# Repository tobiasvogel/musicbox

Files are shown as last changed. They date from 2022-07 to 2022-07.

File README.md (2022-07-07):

# MIDI Music Box

This is an improved version of the original musicbox project by [mitxela](https://github.com/mitxela/musicbox).

There are two major enhancements over the original version:
 - PCBs (Gerber and EAGLE) for the circuits as well as most of the mechanical parts
 - A (optional) addon-board featuring a Arduino MKR WiFi 1010 providing MIDI-file support from both microSD-cards and via WiFi (Webbrowser)

In the future I will furthermore add:
 * *BOM for all PCBs* (work-in-progress)
 * Renderings for visualization
 * Detailed assembly instructions

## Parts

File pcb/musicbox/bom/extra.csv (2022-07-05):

Part | Value | Package | Description | DIGIKEY_PART_NUMBER | FARNELL_PART_NUMBER | MANUFACTURER_NAME | MOUSER_PART_NUMBER
*J2 |  |  | Wire Housings HSG 3P WITH LKG RAMP | WM2012-ND | 1462834 | Molex | 538-22-01-2037
*J3 |  |  | Wire Housings HSG 2P WITH LKG RAMP | WM2011-ND | 1654528 | Molex | 538-22-01-2027
*J4 |  |  | Wire Housings HSG 2P WITH LKG RAMP | WM2011-ND | 1654528 | Molex | 538-22-01-2027
*J5 |  |  | Wire Housings HSG 5P WITH LKG RAMP | WM2014-ND | 1756788 | Molex | 538-22-01-2057
*OK1 |  | DIP08 | 8P IC SOCKET | 609-4717-ND | 2668407 | Amphenol FCI | 649-DILB8P223TLF
*SV1 | Servos 01-15 | Female IDC Socket | HARTING | 0918516681358U-ND | 1106729 | Harting | 617-09-18-516-6813
*SV2 | Servos 16-30 | Female IDC Socket | HARTING | 0918516681358U-ND | 1106729 | Harting | 617-09-18-516-6813
*SV1 | Servos 01-15 | 16P | 3M IDC Flat Cable | 3M157816-1-ND |  | 3M | 3365/16-CUT-LENGTH
*SV2 | Servos 16-30 | 16P | 3M IDC Flat Cable | 3M157816-1-ND |  | 3M | 3365/16-CUT-LENGTH
*U$1 |  | SIP20 | 20P SIP SOCKET | 952-1905-ND | 7991967 | Harwin | 855-M20-7822046
*U$1 |  | SIP20 | 20P SIP SOCKET | 952-1905-ND | 7991967 | Harwin | 855-M20-7822046
*U$1 |  | SIP4 | 4P SIP SOCKET | 952-1792-ND | 7991932 | Harwin | 855-M20-7820446
*ST-LINK |  |  |  | 952-2276-ND | 3395117 | Harwin | 855-M22-2010505

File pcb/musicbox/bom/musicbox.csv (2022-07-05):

Part | Value | Package | Description | DIGIKEY_PART_NUMBER | FARNELL_PART_NUMBER | MANUFACTURER_NAME | MOUSER_PART_NUMBER
C1 | 100nF | C025-025X050 | CAPACITOR, European symbol | BC5142-ND | 2112909 | Vishay / BC Components | 594-K104M15X7RF53L2
D1 | 1N4148 | DO35-7 | DIODE | 1N4148FS-ND | 2322485 | Onsemi / Fairchild | 512-1N4148
D2 | 1N4004 | DO41-10 | DIODE | 1N4004MSCT-ND | 1843708 | Rectron | 583-1N4004-T
J1 | 1727010 | 1727010 | Conn PC Terminal Block 2 POS 3.81mm Solder ST Thru-Hole 13.5A | 277-1947-ND | 3704579 | Phoenix Contact | 651-1727010
J2 | 22-27-2031-03 | 6410-03 | CONNECTOR | WM4112-ND | 9731156 | Molex | 538-22-27-2031
J3 | 22-27-2021-02 | 6410-02 | CONNECTOR | WM4111-ND | 9731148 | Molex | 538-22-27-2021
J4 | 22-27-2021-02 | 6410-02 | CONNECTOR | WM4111-ND | 9731148 | Molex | 538-22-27-2021
J5 | 22-27-2051-05 | 6410-05 | CONNECTOR | WM4114-ND | 9731679 | Molex | 538-22-27-2051
JP1 | HANDLE-MOTOR | 1X03 | PIN HEADER | 68004-403-ND | 3881564 | Amphenol FCI | 651-1012937890301BLF
OK1 | 6N137 | DIL08 | MOTOROLA OPTO COUPLER | 160-1791-ND | 1328376 | Lite-On | 859-6N137
R1 | 220? | 0207/7 | RESISTOR, European symbol | BC3666CT-ND | 3546954 | Vishay / Beyschlag | 594-MBB02070C2200FCT
R2 | 470? | 0207/7 | RESISTOR, European symbol | BC3790CT-ND | 3547014 | Vishay / Beyschlag | 594-MBB02070C4700FCT
ST-LINK | M22-7130542 | RHDR5W50P0X200_1X5_1050X240X44 | 2mm pitch, SIL vertical socket assembly, 5 position | 952-1352-5-ND | 1109729 | Harwin | 855-M22-7130542
SV1 | Servos 01-15 | ML16 | HARTING | 1195-1694-ND | 1106834 | Harting | 617-09185166324
SV2 | Servos 16-30 | ML16 | HARTING | 1195-1694-ND | 1106834 | Harting | 617-09185166324
T1 | 2N2222 | TO92 | NPN TRANSISTOR | KSP2222ABUFS-ND | 1700711 | Diotec Semiconductors | 637-2N2222A
U$1 | STM32F103C8T6 | STM32F103C8T6 | Blue Pill Development Board

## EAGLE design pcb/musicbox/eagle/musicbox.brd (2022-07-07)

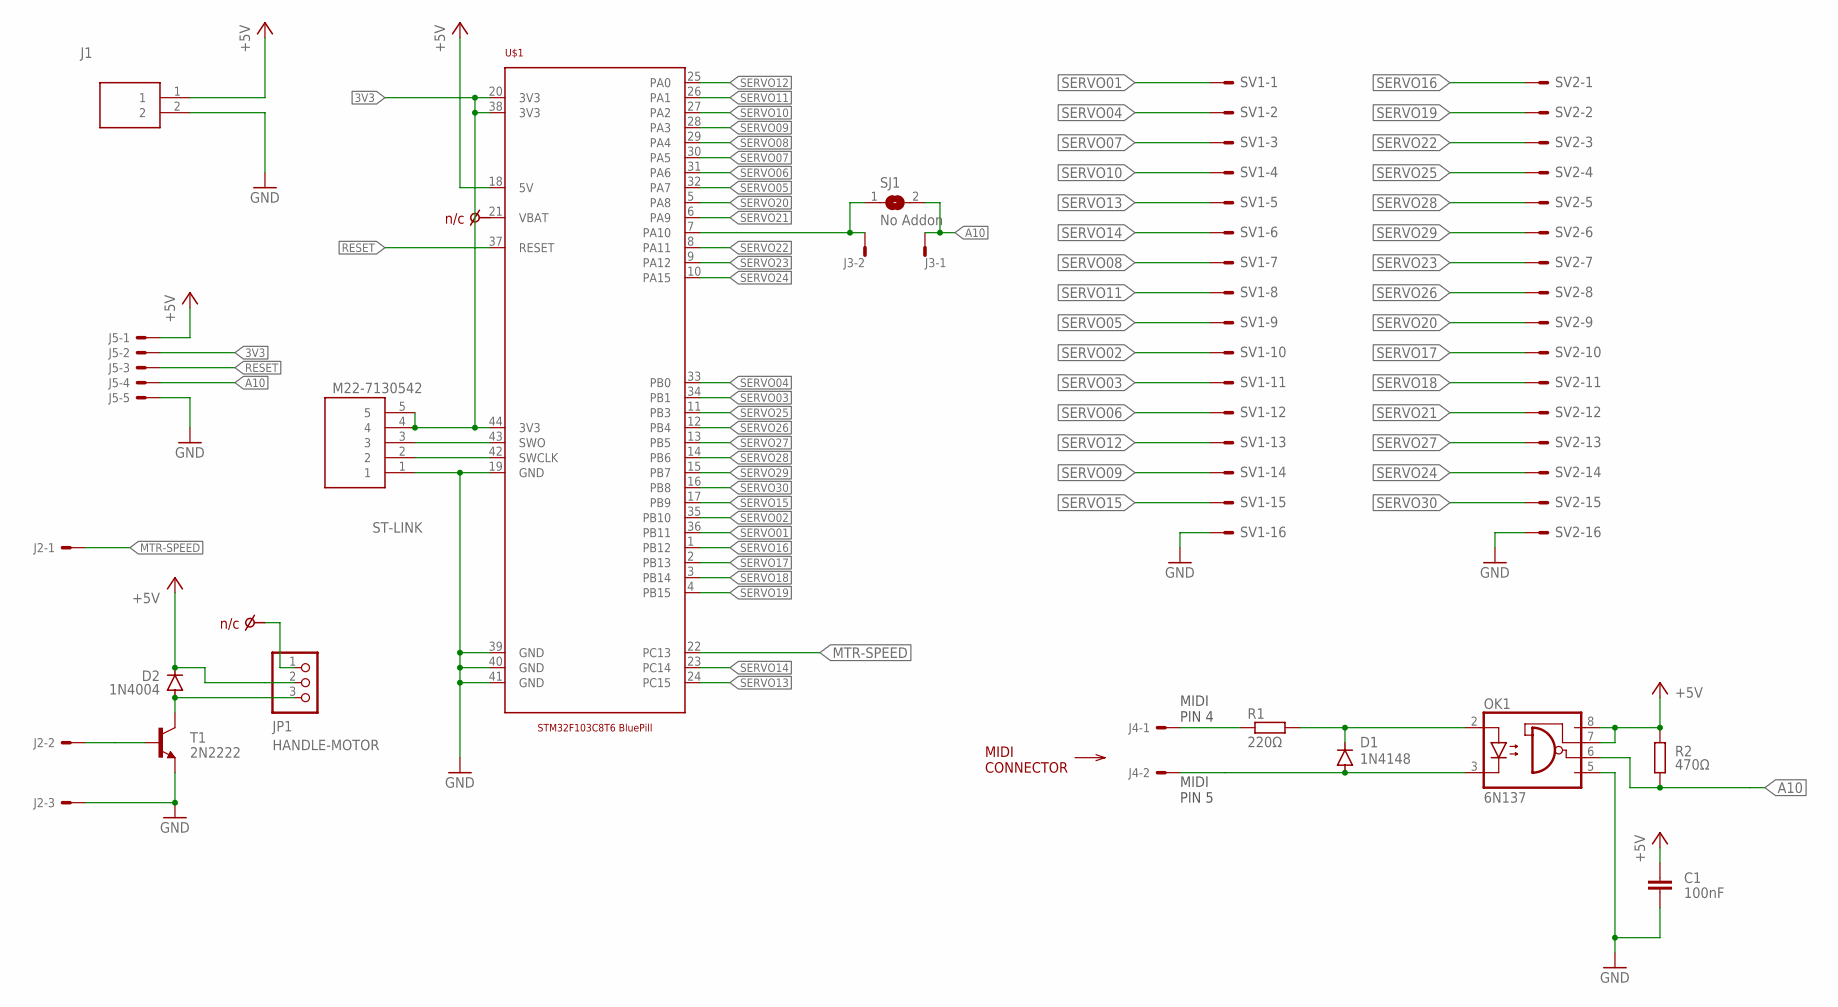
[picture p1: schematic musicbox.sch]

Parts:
C1: 100nF; C025-025X050; MOUSER_PART_NUMBER 594-K104M15X7RF53L2; DIGIKEY_PART_NUMBER BC5142-ND
D1: 1N4148; DO35-7; MOUSER_PART_NUMBER 512-1N4148; DIGIKEY_PART_NUMBER 1N4148FS-ND
D2: 1N4004; DO41-10; MOUSER_PART_NUMBER 583-1N4004-T; DIGIKEY_PART_NUMBER 1N4004MSCT-ND
J1: 1727010; DIGIKEY_PART_NUMBER 277-1947-ND
J2: 22-27-2031-03; 6410-03; MOUSER_PART_NUMBER 538-22-27-2031; DIGIKEY_PART_NUMBER WM4112-ND
J3, J4: 22-27-2021-02; 6410-02; MOUSER_PART_NUMBER 538-22-27-2021; DIGIKEY_PART_NUMBER WM4111-ND
J5: 22-27-2051-05; 6410-05; MOUSER_PART_NUMBER 538-22-27-2051; DIGIKEY_PART_NUMBER WM4114-ND
JP1: HANDLE-MOTOR; 1X03; MOUSER_PART_NUMBER 651-1012937890301BLF; DIGIKEY_PART_NUMBER 68004-403-ND
OK1: 6N137; DIL08; MOUSER_PART_NUMBER 859-6N137; DIGIKEY_PART_NUMBER 160-1791-ND
R1: 220Ω; 0207/7; MOUSER_PART_NUMBER 594-MBB02070C2200FCT; DIGIKEY_PART_NUMBER BC3666CT-ND
R2: 470Ω; 0207/7; MOUSER_PART_NUMBER 594-MBB02070C4700FCT; DIGIKEY_PART_NUMBER BC3790CT-ND
SJ1: No Addon; SJW
ST-LINK: M22-7130542; RHDR5W50P0X200_1X5_1050X240X44; DIGIKEY_PART_NUMBER 952-1352-5-ND
SV1: Servos 01-15; ML16; MOUSER_PART_NUMBER 617-09185166324; DIGIKEY_PART_NUMBER 1195-1694-ND
SV2: Servos 16-30; ML16; MOUSER_PART_NUMBER 617-09185166324; DIGIKEY_PART_NUMBER 1195-1694-ND
T1: 2N2222; TO92; MOUSER_PART_NUMBER 637-2N2222A; DIGIKEY_PART_NUMBER KSP2222ABUFS-ND
U$1: STM32F103C8T6BLUEPILL; STM32F103C8T6

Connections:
3V3: J5.2, ST-LINK.4, ST-LINK.5, U$1.20 (3V3), U$1.38 (3V3), U$1.44 (3V3)
+5V: C1.1, D2.C, J1.1, J5.1, JP1.2, OK1.7 (VE), OK1.8 (VCC), R2.2, U$1.18 (5V)
A10: J3.1, J5.4, OK1.6 (VO), R2.1, SJ1.2
CLK: ST-LINK.2, U$1.42 (SWCLK)
DIO: ST-LINK.3, U$1.43 (SWO)
GND: C1.2, J1.2, J2.3, J5.5, OK1.5 (GND), ST-LINK.1, SV1.16, SV2.16, T1.3 (E), U$1.19 (GND), U$1.39 (GND), U$1.40 (GND), U$1.41 (GND)
MTR-SPEED: J2.1, U$1.22 (PC13)
unnamed: J2.2, T1.2 (B)
unnamed: J4.1, R1.1
unnamed: D2.A, JP1.3, T1.1 (C)
unnamed: D1.A, J4.2, OK1.3 (C)
unnamed: D1.C, OK1.2 (A), R1.2
unnamed: J3.2, SJ1.1, U$1.7 (PA10)
RESET: J5.3, U$1.37 (RESET)
SERVO01: SV1.1, U$1.36 (PB11)
SERVO02: SV1.10, U$1.35 (PB10)
SERVO03: SV1.11, U$1.34 (PB1)
SERVO04: SV1.2, U$1.33 (PB0)
SERVO05: SV1.9, U$1.32 (PA7)
SERVO06: SV1.12, U$1.31 (PA6)
SERVO07: SV1.3, U$1.30 (PA5)
SERVO08: SV1.7, U$1.29 (PA4)
SERVO09: SV1.14, U$1.28 (PA3)
SERVO10: SV1.4, U$1.27 (PA2)
SERVO11: SV1.8, U$1.26 (PA1)
SERVO12: SV1.13, U$1.25 (PA0)
SERVO13: SV1.5, U$1.24 (PC15)
SERVO14: SV1.6, U$1.23 (PC14)
SERVO15: SV1.15, U$1.17 (PB9)
SERVO16: SV2.1, U$1.1 (PB12)
SERVO17: SV2.10, U$1.2 (PB13)
SERVO18: SV2.11, U$1.3 (PB14)
SERVO19: SV2.2, U$1.4 (PB15)
SERVO20: SV2.9, U$1.5 (PA8)
SERVO21: SV2.12, U$1.6 (PA9)
SERVO22: SV2.3, U$1.8 (PA11)
SERVO23: SV2.7, U$1.9 (PA12)
SERVO24: SV2.14, U$1.10 (PA15)
SERVO25: SV2.4, U$1.11 (PB3)
SERVO26: SV2.8, U$1.12 (PB4)
SERVO27: SV2.13, U$1.13 (PB5)
SERVO28: SV2.5, U$1.14 (PB6)
SERVO29: SV2.6, U$1.15 (PB7)
SERVO30: SV2.15, U$1.16 (PB8)

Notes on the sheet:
MIDI PIN 5
MIDI PIN 4
MIDI CONNECTOR

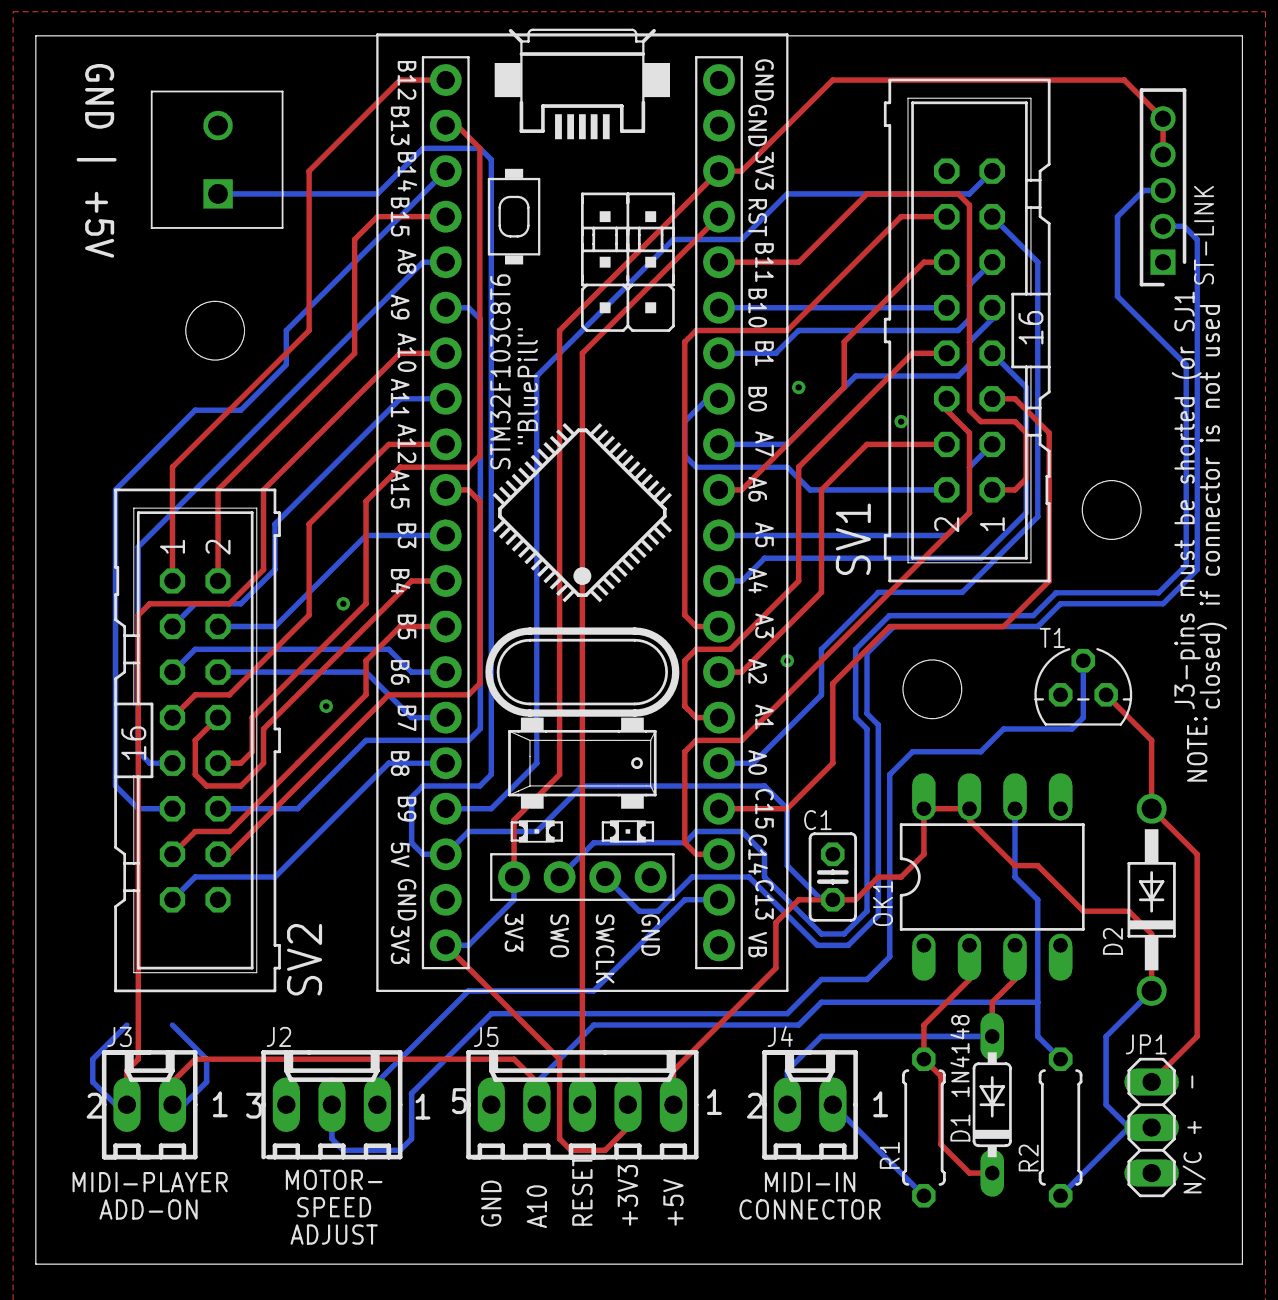
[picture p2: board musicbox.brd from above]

Board: 2 copper layers, 67.3 x 68.5 mm, 18 parts (1 on the bottom side), 44 nets.

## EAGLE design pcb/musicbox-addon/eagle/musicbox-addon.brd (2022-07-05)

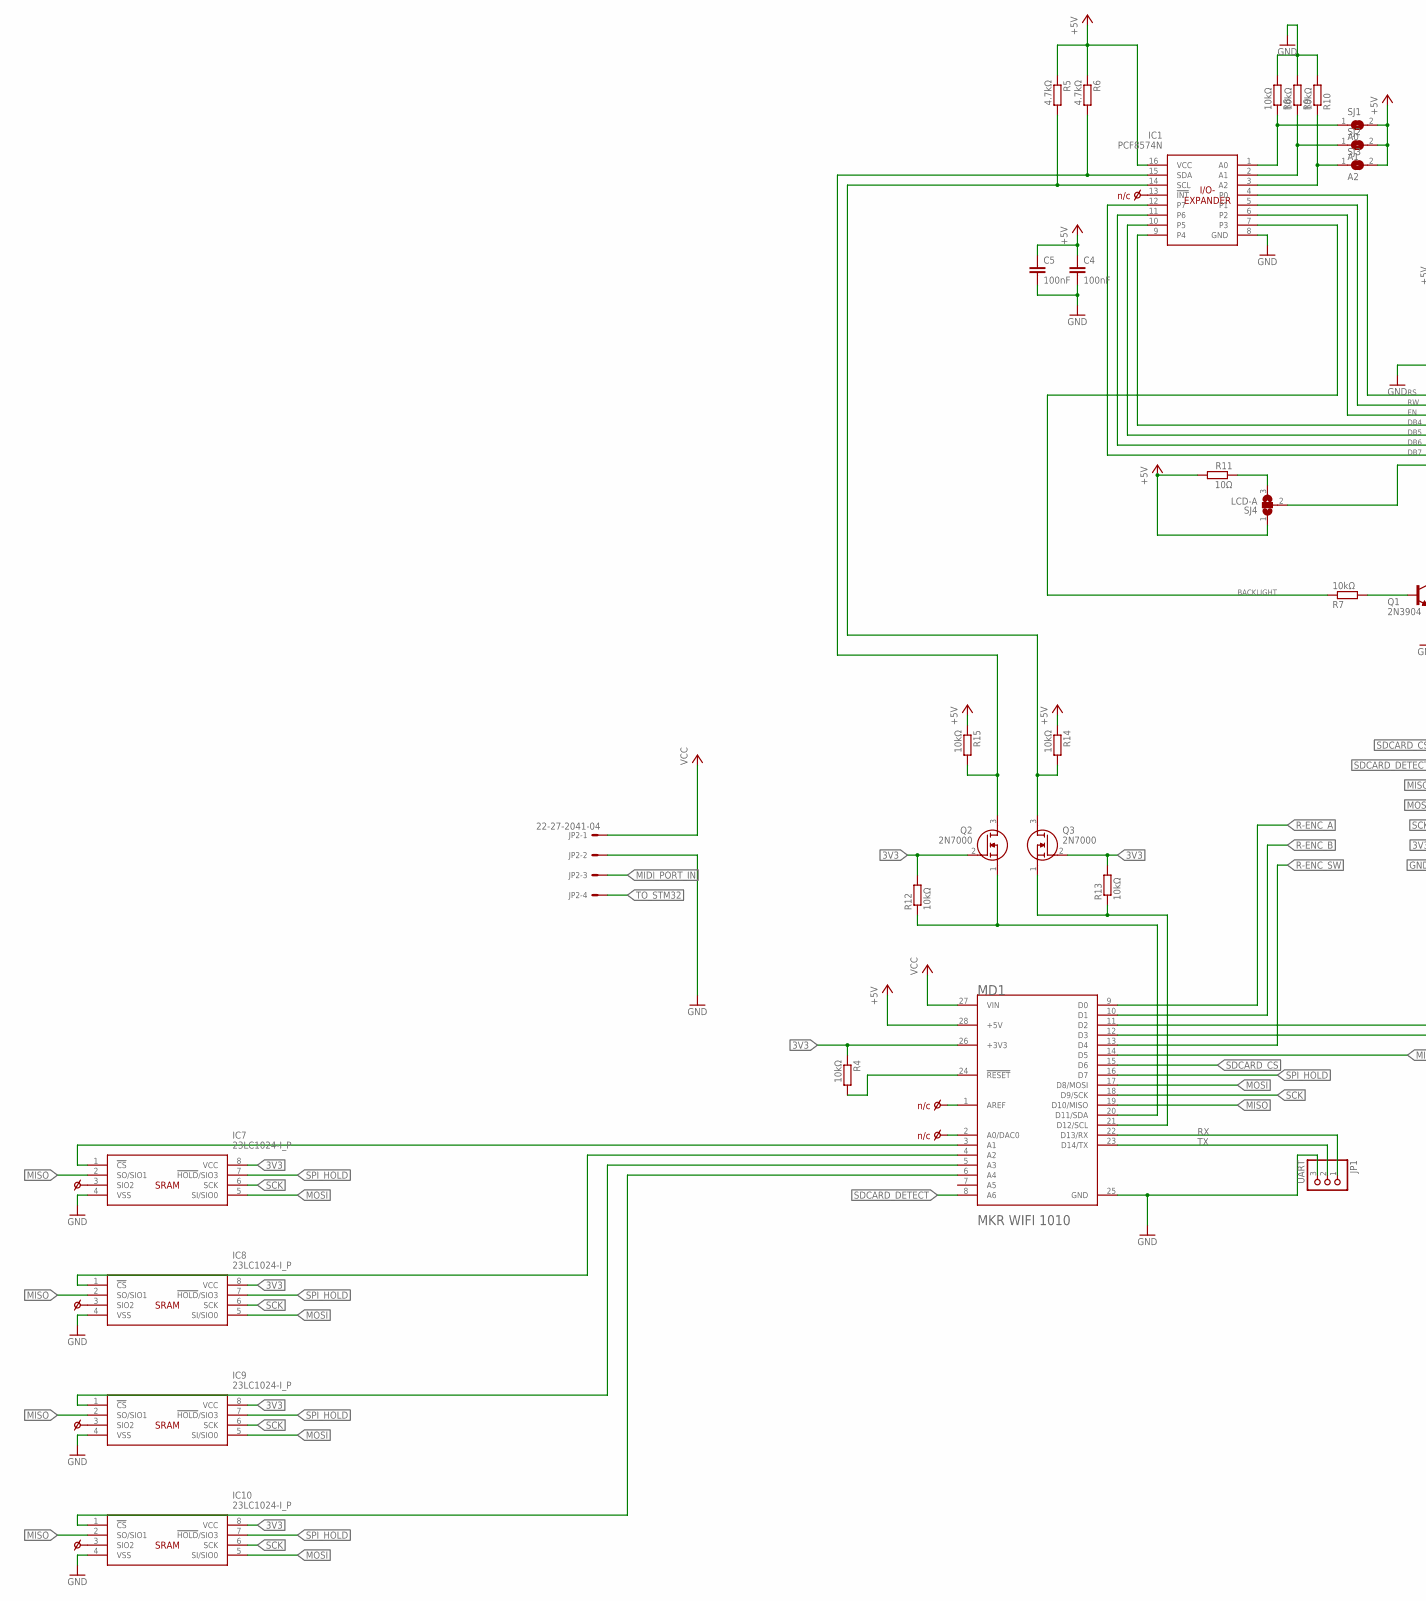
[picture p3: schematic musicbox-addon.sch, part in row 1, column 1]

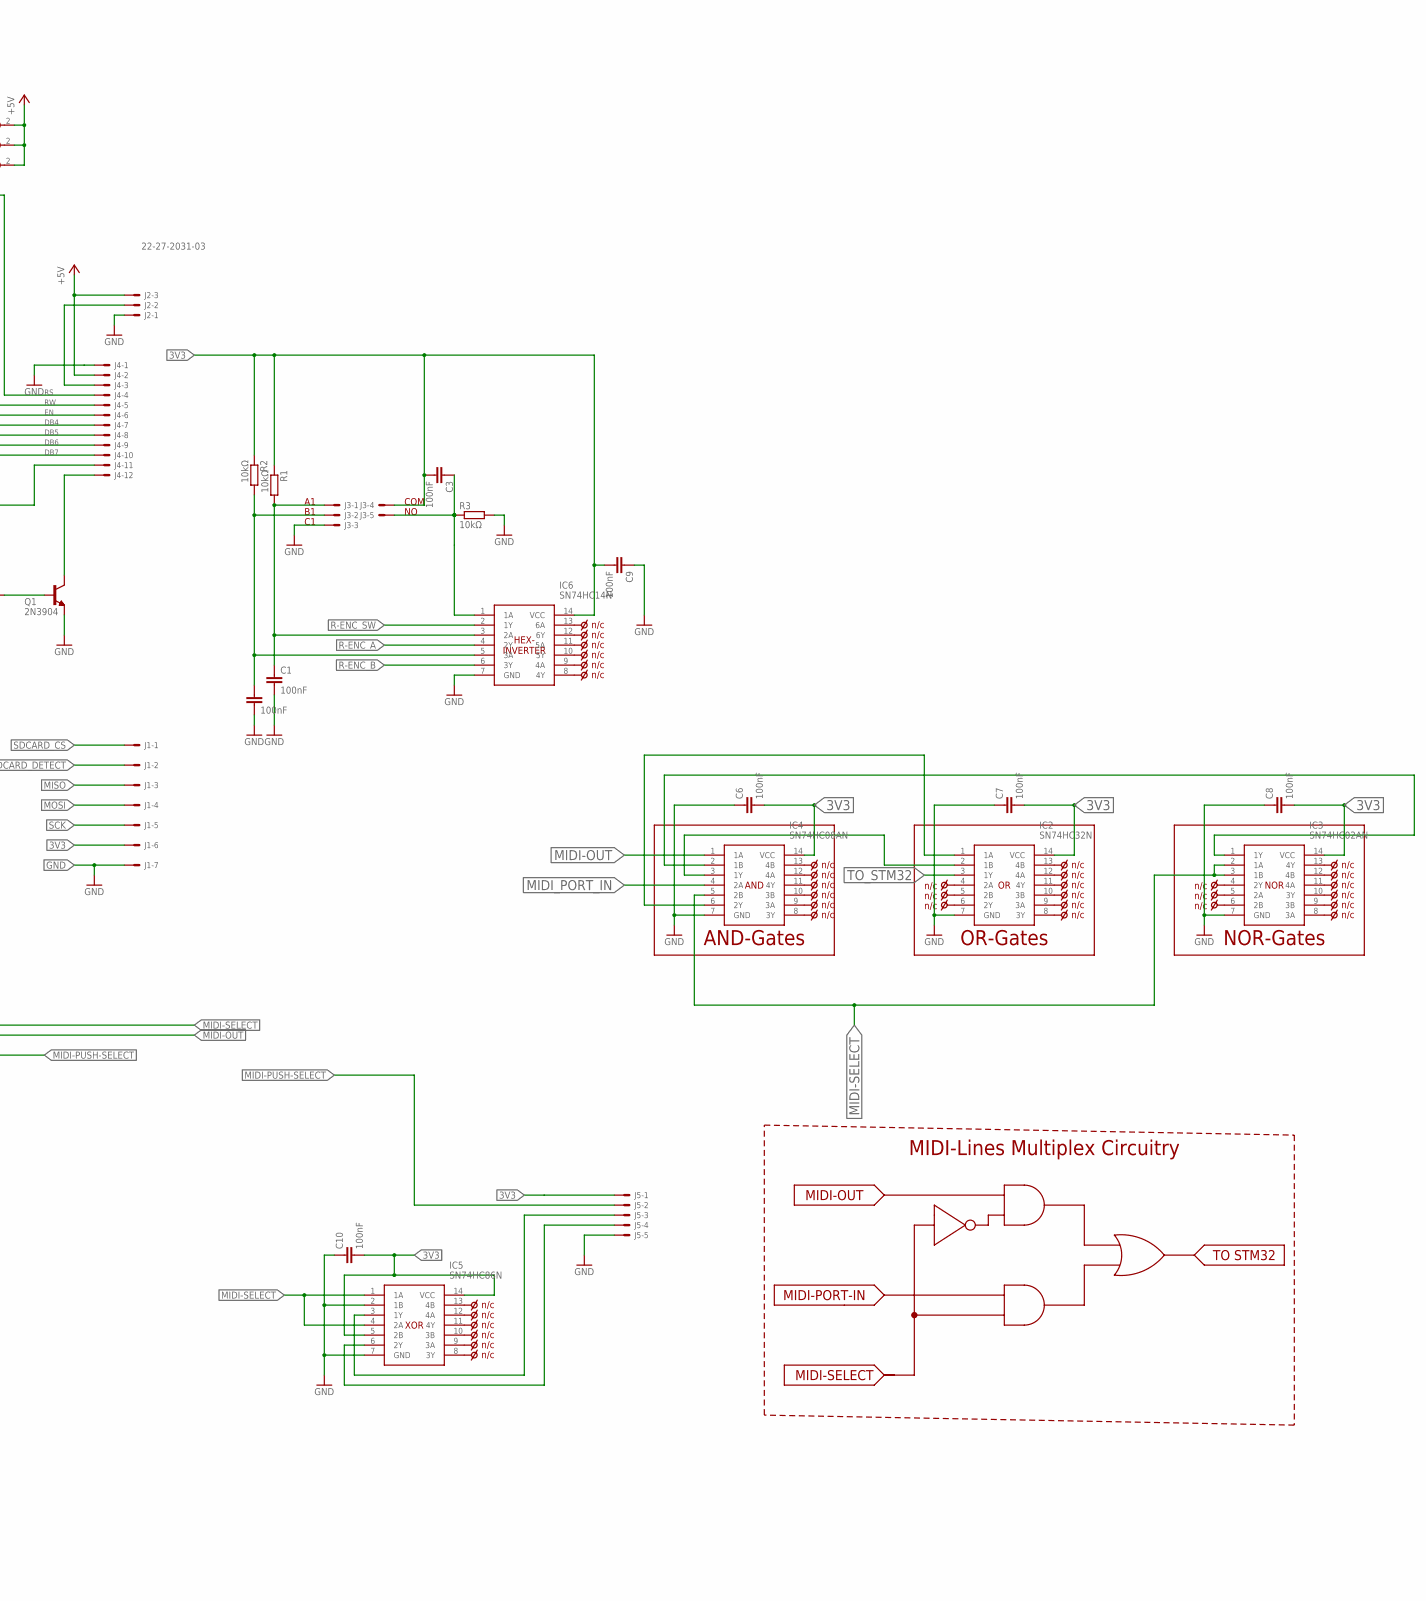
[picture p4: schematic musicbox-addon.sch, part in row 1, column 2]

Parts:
C1, C2, C3, C4, C5, C6, C7, C8, C9, C10: 100nF; C025-025X050; MOUSER_PART_NUMBER 594-K104M15X7RF53L2; DIGIKEY_PART_NUMBER BC5142-ND
IC1: PCF8574N; DIP794W53P254L1930H508Q16N; DIGIKEY_PART_NUMBER 296-13109-5-ND
IC2: SN74HC32N; DIP794W53P254L1930H508Q14N; DIGIKEY_PART_NUMBER 296-1589-5-ND
IC3: SN74HC02AN; DIP794W53P254L1930H508Q14N; DIGIKEY_PART_NUMBER 296-SN74HC02AN-ND
IC4: SN74HC08AN; DIP794W53P254L1930H508Q14N; DIGIKEY_PART_NUMBER 296-1570-5-ND
IC5: SN74HC86N; DIP794W53P254L1930H508Q14N; DIGIKEY_PART_NUMBER 296-8375-5-ND
IC6: SN74HC14N; DIP794W53P254L1930H508Q14N; DIGIKEY_PART_NUMBER 296-1577-5-ND
IC7, IC8, IC9, IC10: 23LC1024-I_P; DIP781W56P254L950H533Q8N; DIGIKEY_PART_NUMBER 23LC1024-I/P-ND
J1: 22-27-2071-07; 6410-07; MOUSER_PART_NUMBER 538-22-27-2071; DIGIKEY_PART_NUMBER WM4116-ND
J2: 22-27-2031-03; 6410-03; MOUSER_PART_NUMBER 538-22-27-2031; DIGIKEY_PART_NUMBER WM4112-ND
J3, J5: 22-27-2051-05; 6410-05; MOUSER_PART_NUMBER 538-22-27-2051; DIGIKEY_PART_NUMBER WM4114-ND
J4: 22-27-2121-12; 6410-12; MOUSER_PART_NUMBER 538-22-27-2121; DIGIKEY_PART_NUMBER 23-0022272121-ND
JP1: UART; 1X03; MOUSER_PART_NUMBER 649-1012937890301BLF; DIGIKEY_PART_NUMBER 68002-403-ND
JP2: 22-27-2041-04; 6410-04
MD1: ARDUINO_MKR_WIFI_1010ARDUINO_MKR_WIFI_1010_0_0; ARDUINO_MKR_WIFI_1010_0; FARNELL_PART_NUMBER 2917569
Q1: 2N3904; TO92; MOUSER_PART_NUMBER 610-2N3904; DIGIKEY_PART_NUMBER 1514-2N3904PBFREE-ND
Q2, Q3: 2N7000; TO-92_(TO-226); DIGIKEY_PART_NUMBER 2N7000FS-ND
R1, R2, R3, R4, R7, R8, R9, R10, R12, R13, R14, R15: 10kΩ; 0207/7; MOUSER_PART_NUMBER 594-MBB02070C1002FCT; DIGIKEY_PART_NUMBER BC3569CT-ND
R5, R6: 4.7kΩ; 0207/7; MOUSER_PART_NUMBER 594-MBB02070C4701FCT; DIGIKEY_PART_NUMBER BC3792CT-ND
R11: 10Ω; 0207/7; MOUSER_PART_NUMBER 594-MBB02070C3300FCT; DIGIKEY_PART_NUMBER BC3741CT-ND
SJ1: A0; SJ
SJ2: A1; SJ
SJ3: A2; SJ
SJ4: LCD-A; SJ_2

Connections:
3V3: C3.2, C6.2, C7.2, C8.2, C9.2, C10.2, IC2.14 (VCC), IC3.14 (VCC), IC4.14 (VCC), IC5.5 (2B), IC5.14 (VCC), IC6.14 (VCC), IC7.8 (VCC), IC8.8 (VCC), IC9.8 (VCC), IC10.8 (VCC), J1.6, J3.4, J5.1, MD1.26 (+3V3), Q2.2 (G), Q3.2 (G), R1.1, R2.1, R4.1, R12.2, R13.2
+5V: C4.1, C5.1, IC1.16 (VCC), J2.3, J4.2, MD1.28 (+5V), R5.1, R6.1, R11.2, R14.1, R15.1, SJ1.2, SJ2.2, SJ3.2, SJ4.1
BACKLIGHT: IC1.7 (P3), R7.1
DB4: IC1.9 (P4), J4.7
DB5: IC1.10 (P5), J4.8
DB6: IC1.11 (P6), J4.9
DB7: IC1.12 (P7), J4.10
EN: IC1.6 (P2), J4.6
GND: C1.2, C2.2, C4.2, C5.2, C6.1, C7.1, C8.1, C9.1, C10.1, IC1.8 (GND), IC2.7 (GND), IC3.7 (GND), IC4.7 (GND), IC5.2 (1B), IC5.7 (GND), IC6.7 (GND), IC7.4 (VSS), IC8.4 (VSS), IC9.4 (VSS), IC10.4 (VSS), J1.7, J2.1, J3.3, J4.1, J5.5, JP1.3, JP2.2, MD1.25 (GND), Q1.3 (E), R3.2, R8.2, R9.2, R10.2
I2C_SCL: IC1.14 (SCL), Q3.3 (D), R5.2, R14.2
I2C_SDA: IC1.15 (SDA), Q2.3 (D), R6.2, R15.2
MIDI-OUT: IC4.1 (1A), MD1.12 (D3)
MIDI-PUSH-SELECT: J5.2, MD1.14 (D5)
MIDI-SELECT: IC3.2 (1A), IC3.3 (1B), IC4.5 (2B), IC5.1 (1A), IC5.4 (2A), MD1.11 (D2)
MIDI_PORT_IN: IC4.4 (2A), JP2.3
MISO: IC7.2 (SO/SIO1), IC8.2 (SO/SIO1), IC9.2 (SO/SIO1), IC10.2 (SO/SIO1), J1.3, MD1.19 (D10/MISO)
MOSI: IC7.5 (SI/SIO0), IC8.5 (SI/SIO0), IC9.5 (SI/SIO0), IC10.5 (SI/SIO0), J1.4, MD1.17 (D8/MOSI)
unnamed: IC1.3 (A2), R10.1, SJ3.1
unnamed: IC1.1 (A0), R8.1, SJ1.1
unnamed: IC1.2 (A1), R9.1, SJ2.1
unnamed: C3.1, IC6.1 (1A), J3.5, R3.1
unnamed: MD1.24 (!RESET!), R4.2
unnamed: MD1.21 (D12/SCL), Q3.1 (S), R13.1
unnamed: IC2.2 (1B), IC4.3 (1Y)
unnamed: IC3.1 (1Y), IC4.2 (1B)
unnamed: IC2.1 (1A), IC4.6 (2Y)
unnamed: J4.11, SJ4.2
unnamed: R11.1, SJ4.3
unnamed: IC5.3 (1Y), J5.3
unnamed: IC5.6 (2Y), J5.4
unnamed: MD1.20 (D11/SDA), Q2.1 (S), R12.1
unnamed: Q1.2 (B), R7.2
unnamed: J2.2, J4.3
unnamed: IC7.1 (!CS), MD1.3 (A1)
unnamed: IC8.1 (!CS), MD1.4 (A2)
unnamed: IC9.1 (!CS), MD1.5 (A3)
unnamed: IC10.1 (!CS), MD1.6 (A4)
unnamed: J4.12, Q1.1 (C)
R-ENC_A: IC6.4 (2Y), MD1.9 (D0)
R-ENC_B: IC6.6 (3Y), MD1.10 (D1)
R-ENC_SW: IC6.2 (1Y), MD1.13 (D4)
RS: IC1.4 (P0), J4.4
RW: IC1.5 (P1), J4.5
RX: JP1.1, MD1.22 (D13/RX)
R_ENC_A: C1.1, IC6.3 (2A), J3.1, R1.2
R_ENC_B: C2.1, IC6.5 (3A), J3.2, R2.2
SCK: IC7.6 (SCK), IC8.6 (SCK), IC9.6 (SCK), IC10.6 (SCK), J1.5, MD1.18 (D9/SCK)
SDCARD_CS: J1.1, MD1.15 (D6)
SDCARD_DETECT: J1.2, MD1.8 (A6)
SPI_HOLD: IC7.7 (!HOLD!/SIO3), IC8.7 (!HOLD!/SIO3), IC9.7 (!HOLD!/SIO3), IC10.7 (!HOLD!/SIO3), MD1.16 (D7)
TO_STM32: IC2.3 (1Y), JP2.4
TX: JP1.2, MD1.23 (D14/TX)
VCC: JP2.1, MD1.27 (VIN)

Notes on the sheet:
AND-Gates
OR-Gates
NOR-Gates
MIDI-Lines Multiplex Circuitry
MIDI-OUT
MIDI-PORT-IN
TO STM32
MIDI-SELECT
COM
XOR
AND
NOR
HEX- INVERTER
I/O- EXPANDER
SRAM

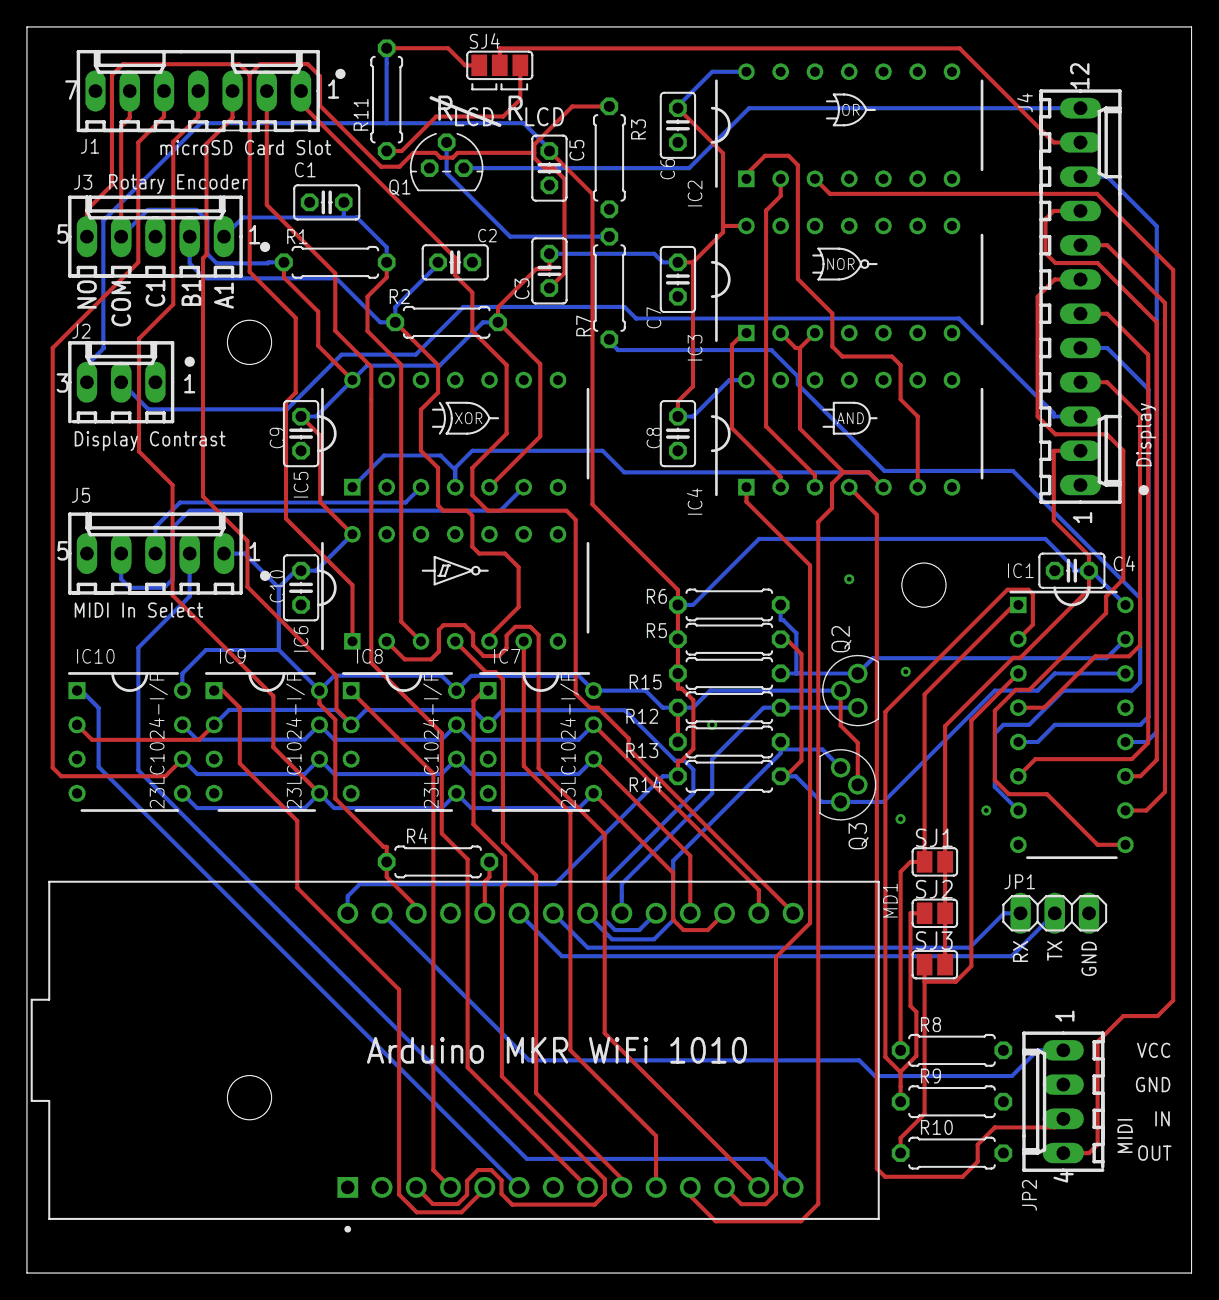
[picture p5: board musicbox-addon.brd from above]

Board: 2 copper layers, 86.3 x 92.4 mm, 50 parts (0 on the bottom side), 53 nets.

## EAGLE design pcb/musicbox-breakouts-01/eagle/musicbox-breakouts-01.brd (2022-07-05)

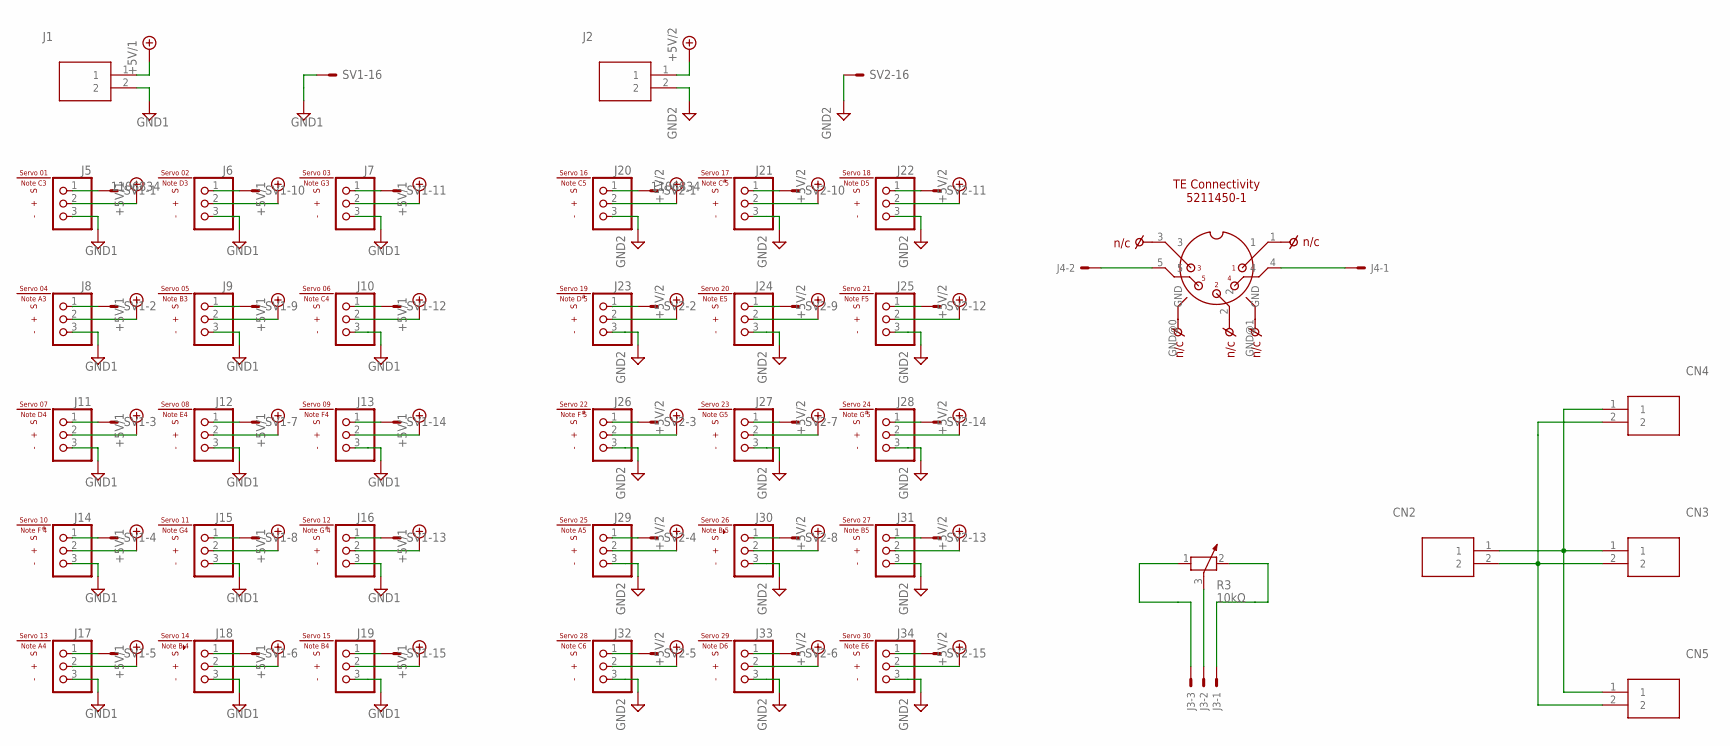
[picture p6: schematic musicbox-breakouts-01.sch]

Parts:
CN1: 5211450-1; MOUSER_PART_NUMBER 571-5211450-1; DIGIKEY_PART_NUMBER 5211450-1-ND
CN2, CN3, CN4, CN5: 1727010; DIGIKEY_PART_NUMBER 277-1947-ND
J1, J2: 1727010; DIGIKEY_PART_NUMBER 277-1947-ND
J3: 22-05-7038-03; 7395-03; MOUSER_PART_NUMBER 538-22-05-7038; DIGIKEY_PART_NUMBER WM2785-ND
J4: 22-27-2021-02; 6410-02; MOUSER_PART_NUMBER 538-22-27-2021; DIGIKEY_PART_NUMBER WM4111-ND
J5, J6, J7, J8, J9, J10, J11, J12, J13, J14, J15, J16, J17, J18, J19, J20, J21, J22, J23, J24, J25, J26, J27, J28, J29, J30, J31, J32, J33, J34: PINHD-1X3; 1X03; MOUSER_PART_NUMBER 649-1012937890301BLF; DIGIKEY_PART_NUMBER 68004-403-ND
R3: 10kΩ; PT-10; MOUSER_PART_NUMBER 531-PT10MV1103A11PMS; DIGIKEY_PART_NUMBER 1993-PT10MV10-103A1010-PM-S-ND
SV1, SV2: ML16E; ML16; MOUSER_PART_NUMBER 617-09185166324; DIGIKEY_PART_NUMBER 1195-1694-ND
U$1, U$2, U$3, U$4, U$5, U$6, U$7, U$8, U$9, U$10, U$11, U$12, U$13, U$14, U$15, U$16, U$17, U$18, U$19, U$20, U$21, U$22, U$23, U$24, U$25, U$26, U$27, U$28, U$29, U$30: SERVO-SMALL
U$41: SERVO01_NOTEC3; SERVO_1/NOTE_C3
U$42: SERVO02_NOTED3; SERVO_2/NOTE_D3
U$43: SERVO03_NOTEG3; SERVO_3/NOTE_G3
U$44: SERVO04_NOTEA3; SERVO_4/NOTE_A3
U$45: SERVO05_NOTEB3; SERVO_5/NOTE_B3
U$46: SERVO06_NOTEC4; SERVO_6/NOTE_C4
U$47: SERVO07_NOTED4; SERVO_7/NOTE_D4
U$48: SERVO08_NOTEE4; SERVO_8/NOTE_E4
U$49: SERVO09_NOTEF4; SERVO_9/NOTE_F4
U$50: SERVO10_NOTEF#4; SERVO_10/NOTE_F#4
U$51: SERVO11_NOTEG4; SERVO_11/NOTE_G4
U$52: SERVO12_NOTEG#4; SERVO_12/NOTE_G#4
U$53: SERVO13_NOTEA4; SERVO_13/NOTE_A4
U$54: SERVO14_NOTEBB4; SERVO_14/NOTE_BB4
U$55: SERVO15_NOTEB4; SERVO_15/NOTE_B4
U$56: SERVO16_NOTEC5; SERVO_16/NOTE_C5
U$57: SERVO17_NOTEC#5; SERVO_17/NOTE_C#5
U$58: SERVO18_NOTED5; SERVO_18/NOTE_D5
U$59: SERVO19_NOTED#5; SERVO_19/NOTE_D#5
U$60: SERVO20_NOTEE5; SERVO_20/NOTE_E5
U$61: SERVO21_NOTEF5; SERVO_21/NOTE_F5
U$62: SERVO22_NOTEF#5; SERVO_22/NOTE_F#5
U$63: SERVO23_NOTEG5; SERVO_23/NOTE_G5
U$64: SERVO24_NOTEG#5; SERVO_24/NOTE_G#5
U$65: SERVO25_NOTEA5; SERVO_25/NOTE_A5
U$66: SERVO26_NOTEBB5; SERVO_26/NOTE_BB5
U$67: SERVO27_NOTEB5; SERVO_27/NOTE_B5
U$69: SERVO28_NOTEC6; SERVO_28/NOTE_C6
U$70: SERVO29_NOTED6; SERVO_29/NOTE_D6
U$71: SERVO30_NOTEE6; SERVO_30/NOTE_E6

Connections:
+5V: J1.1, J5.2, J6.2, J7.2, J8.2, J9.2, J10.2, J11.2, J12.2, J13.2, J14.2, J15.2, J16.2, J17.2, J18.2, J19.2
GND: J1.2, J5.3, J6.3, J7.3, J8.3, J9.3, J10.3, J11.3, J12.3, J13.3, J14.3, J15.3, J16.3, J17.3, J18.3, J19.3, SV1.16
unnamed: J5.1, SV1.1
unnamed: J8.1, SV1.2
unnamed: J11.1, SV1.3
unnamed: J14.1, SV1.4
unnamed: J17.1, SV1.5
unnamed: J16.1, SV1.13
unnamed: J19.1, SV1.15
unnamed: J13.1, SV1.14
unnamed: J10.1, SV1.12
unnamed: J7.1, SV1.11
unnamed: J6.1, SV1.10
unnamed: J9.1, SV1.9
unnamed: J12.1, SV1.7
unnamed: J15.1, SV1.8
unnamed: J18.1, SV1.6
unnamed: J20.1, SV2.1
unnamed: J21.1, SV2.10
unnamed: J22.1, SV2.11
unnamed: J24.1, SV2.9
unnamed: J23.1, SV2.2
unnamed: J25.1, SV2.12
unnamed: J26.1, SV2.3
unnamed: J27.1, SV2.7
unnamed: J28.1, SV2.14
unnamed: J29.1, SV2.4
unnamed: J30.1, SV2.8
unnamed: J31.1, SV2.13
unnamed: J32.1, SV2.5
unnamed: J33.1, SV2.6
unnamed: J34.1, SV2.15
unnamed: CN2.1, CN3.1, CN4.1, CN5.1
unnamed: CN2.2, CN3.2, CN4.2, CN5.2
unnamed: J3.3, R3.1
unnamed: J3.2, R3.3
unnamed: J3.1, R3.2
unnamed: CN1.4, J4.1
unnamed: CN1.5, J4.2
VCC: J2.1, J20.2, J21.2, J22.2, J23.2, J24.2, J25.2, J26.2, J27.2, J28.2, J29.2, J30.2, J31.2, J32.2, J33.2, J34.2
VSS: J2.2, J20.3, J21.3, J22.3, J23.3, J24.3, J25.3, J26.3, J27.3, J28.3, J29.3, J30.3, J31.3, J32.3, J33.3, J34.3, SV2.16

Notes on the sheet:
TE Connectivity 5211450-1

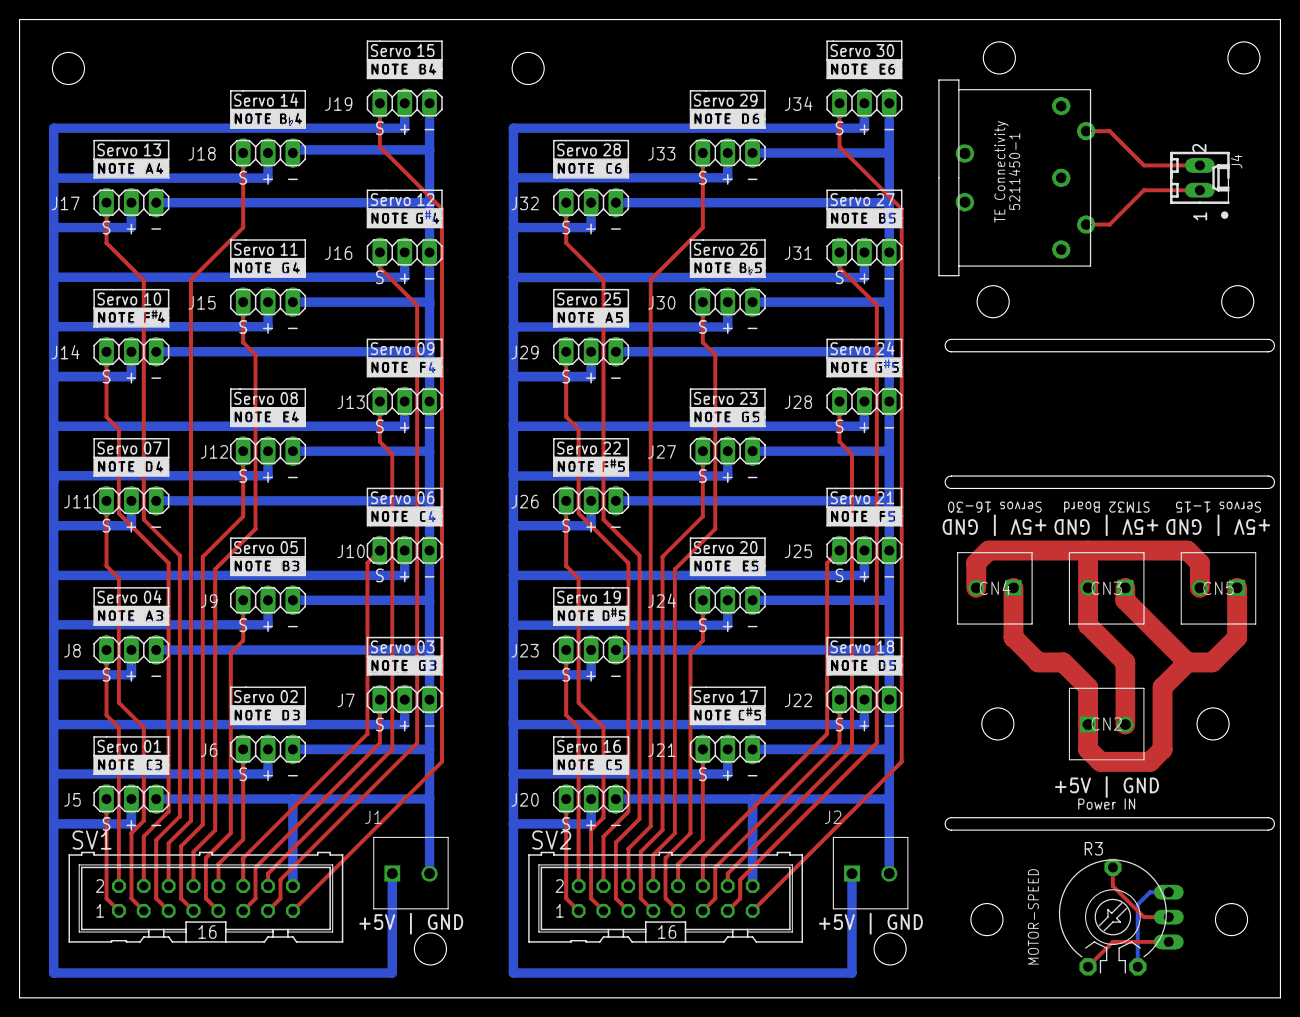
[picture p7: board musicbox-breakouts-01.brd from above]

Board: 2 copper layers, 128.9 x 100.0 mm, 102 parts (1 on the bottom side), 41 nets.

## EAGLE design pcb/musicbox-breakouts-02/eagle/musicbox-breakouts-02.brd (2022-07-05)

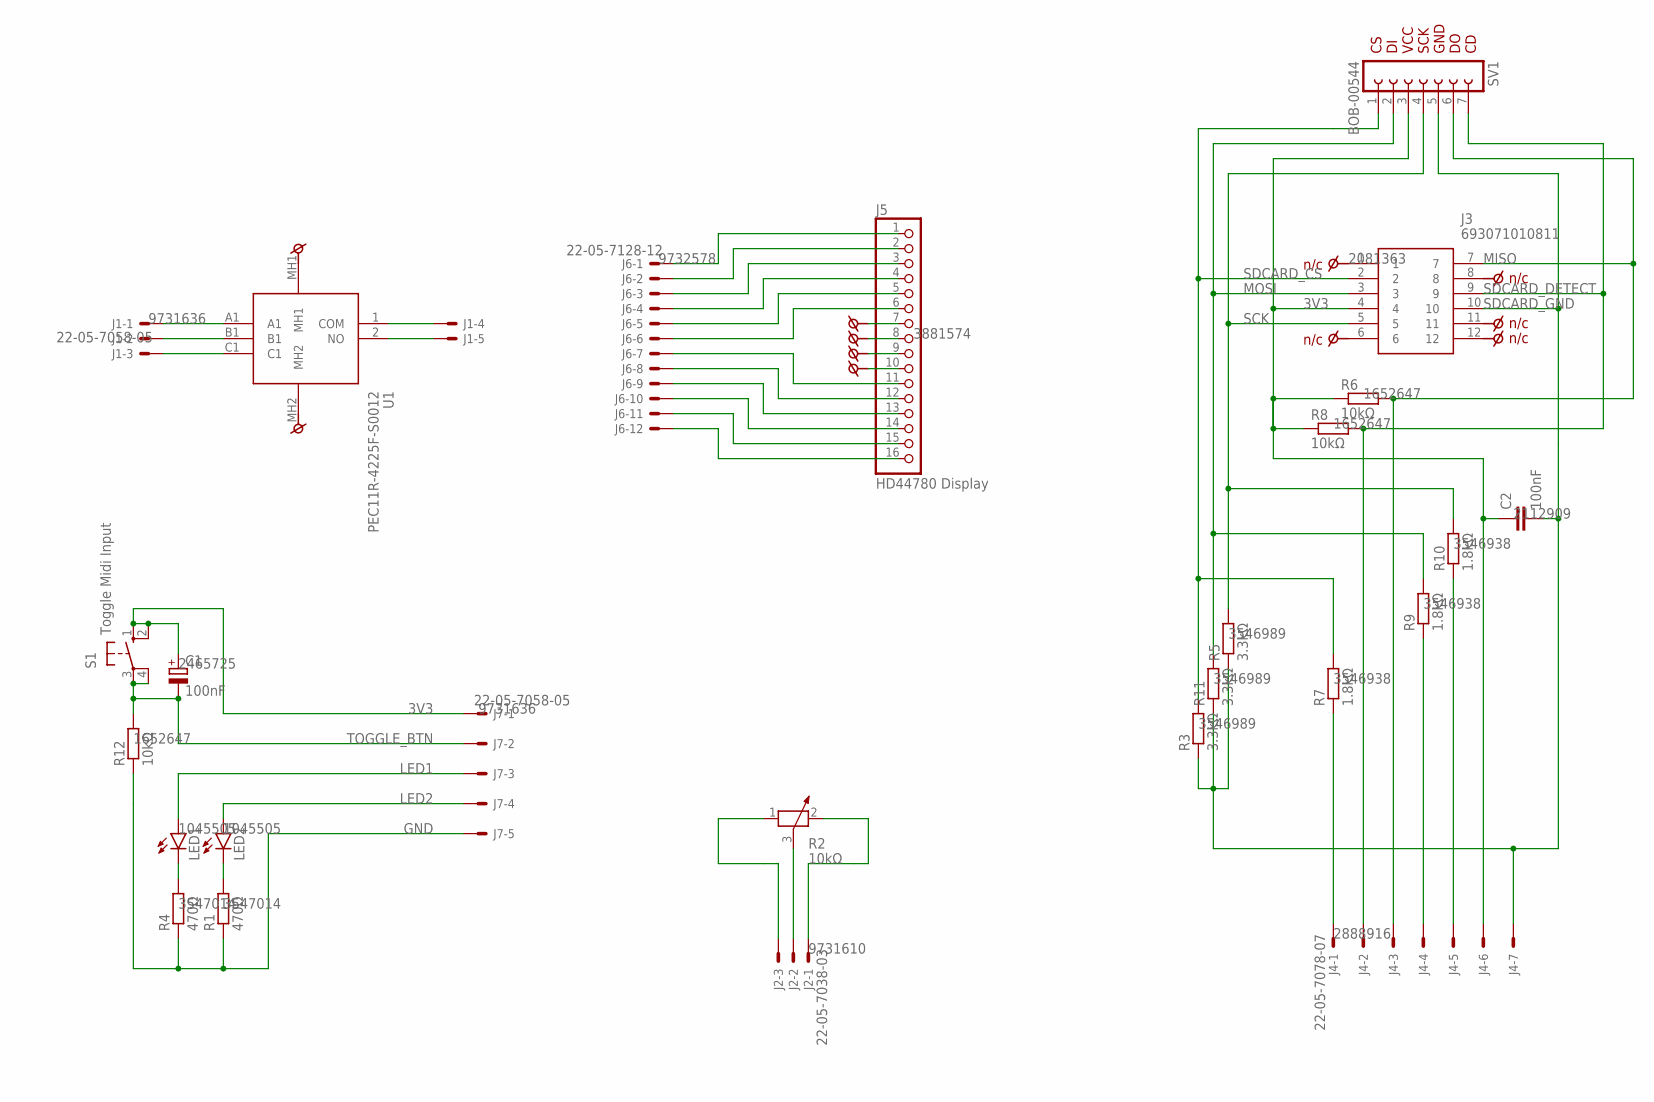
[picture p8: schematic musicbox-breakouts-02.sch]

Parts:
C1: 100nF; E1,8-4; MOUSER_PART_NUMBER 710-860010672001; DIGIKEY_PART_NUMBER 732-8653-1-ND
C2: 100nF; C025-025X050; MOUSER_PART_NUMBER 594-K104M15X7RF53L2; DIGIKEY_PART_NUMBER BC5142-ND
J1, J7: 22-05-7058-05; 7395-05; MOUSER_PART_NUMBER 538-22-05-7058; DIGIKEY_PART_NUMBER WM2787-ND
J2: 22-05-7038-03; 7395-03; MOUSER_PART_NUMBER 538-22-05-7038; DIGIKEY_PART_NUMBER WM2785-ND
J3: 693071010811; DIGIKEY_PART_NUMBER 732-3819-1-ND
J4: 22-05-7078-07; 7395-07; MOUSER_PART_NUMBER 538-22-05-7078; DIGIKEY_PART_NUMBER WM17054-ND
J5: HD44780 Display; 1X16; MOUSER_PART_NUMBER 649-1012937891601BLF; DIGIKEY_PART_NUMBER 68002-116-ND
J6: 22-05-7128-12; 7395-12; MOUSER_PART_NUMBER 538-22-05-7128; DIGIKEY_PART_NUMBER WM4378-ND
LED1, LED2: LED3MM; MOUSER_PART_NUMBER 78-TLLG4401-AS12; DIGIKEY_PART_NUMBER TLLG4401-AS12CT-ND
R1, R4: 470Ω; 0207/7; MOUSER_PART_NUMBER 594-MBB02070C4700FCT; DIGIKEY_PART_NUMBER BC3790CT-ND
R2: 10kΩ; PT-10; MOUSER_PART_NUMBER 531-PT10MV1103A11PMS; DIGIKEY_PART_NUMBER 1993-PT10MV10-103A1010-PM-S-ND
R3, R5, R11: 3.3kΩ; 0207/7; MOUSER_PART_NUMBER 594-MBB02070C3301FCT; DIGIKEY_PART_NUMBER BC3743CT-ND
R6, R8, R12: 10kΩ; 0207/7; MOUSER_PART_NUMBER 594-MBB02070C1002FCT; DIGIKEY_PART_NUMBER BC3569CT-ND
R7, R9, R10: 1.8kΩ; 0207/7; MOUSER_PART_NUMBER 594-MBB02070C1801FCT; DIGIKEY_PART_NUMBER BC3638CT-ND
S1: Toggle Midi Input; B3F-10XX; MOUSER_PART_NUMBER 179-TS0266130BK160LC; DIGIKEY_PART_NUMBER 2223-TS02-66-130-BK-160-LCR-D-ND
SV1: BOB-00544; FE07
U1: PEC11R-4225F-S0012; PEC11R4225FS0012; DIGIKEY_PART_NUMBER PEC11R-4225F-S0012-ND

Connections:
3V3: C2.1, J3.4, J4.6, R6.1, R8.1, SV1.3
DISPLAY_1: J5.1, J6.1
MISO: J3.7, J4.3, R6.2, SV1.6
MOSI: J3.3, R9.2, R11.2, SV1.2
unnamed: J1.1, U1.A1
unnamed: J1.2, U1.B1
unnamed: J1.3, U1.C1
unnamed: J1.5, U1.2 (NO)
unnamed: J1.4, U1.1 (COM)
unnamed: J5.2, J6.2
unnamed: J5.3, J6.3
unnamed: J5.4, J6.4
unnamed: J5.5, J6.5
unnamed: J5.6, J6.6
unnamed: J5.16, J6.12
unnamed: J5.15, J6.11
unnamed: J5.14, J6.10
unnamed: J5.13, J6.9
unnamed: J5.12, J6.8
unnamed: J5.11, J6.7
unnamed: C1.-, J7.2, R12.2, S1.3, S1.4 (P1)
unnamed: J7.3, LED1.A
unnamed: J7.4, LED2.A
unnamed: C1.+, J7.1, S1.1 (S), S1.2 (S1)
unnamed: J7.5, R1.1, R4.1, R12.1
unnamed: LED1.K (C), R4.2
unnamed: LED2.K (C), R1.2
unnamed: J2.3, R2.1
unnamed: J2.2, R2.3
unnamed: J2.1, R2.2
unnamed: J4.1, R7.1
unnamed: J4.5, R10.1
unnamed: J4.4, R9.1
SCK: J3.5, R5.2, R10.2, SV1.4
SDCARD_CS: J3.2, R3.2, R7.2, SV1.1
SDCARD_DETECT: J3.9, J4.2, R8.2, SV1.7
SDCARD_GND: C2.2, J3.10, J4.7, R3.1, R5.1, R11.1, SV1.5

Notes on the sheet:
GND
3V3
TOGGLE_BTN
LED1
LED2
CS DI VCC SCK GND DO CD

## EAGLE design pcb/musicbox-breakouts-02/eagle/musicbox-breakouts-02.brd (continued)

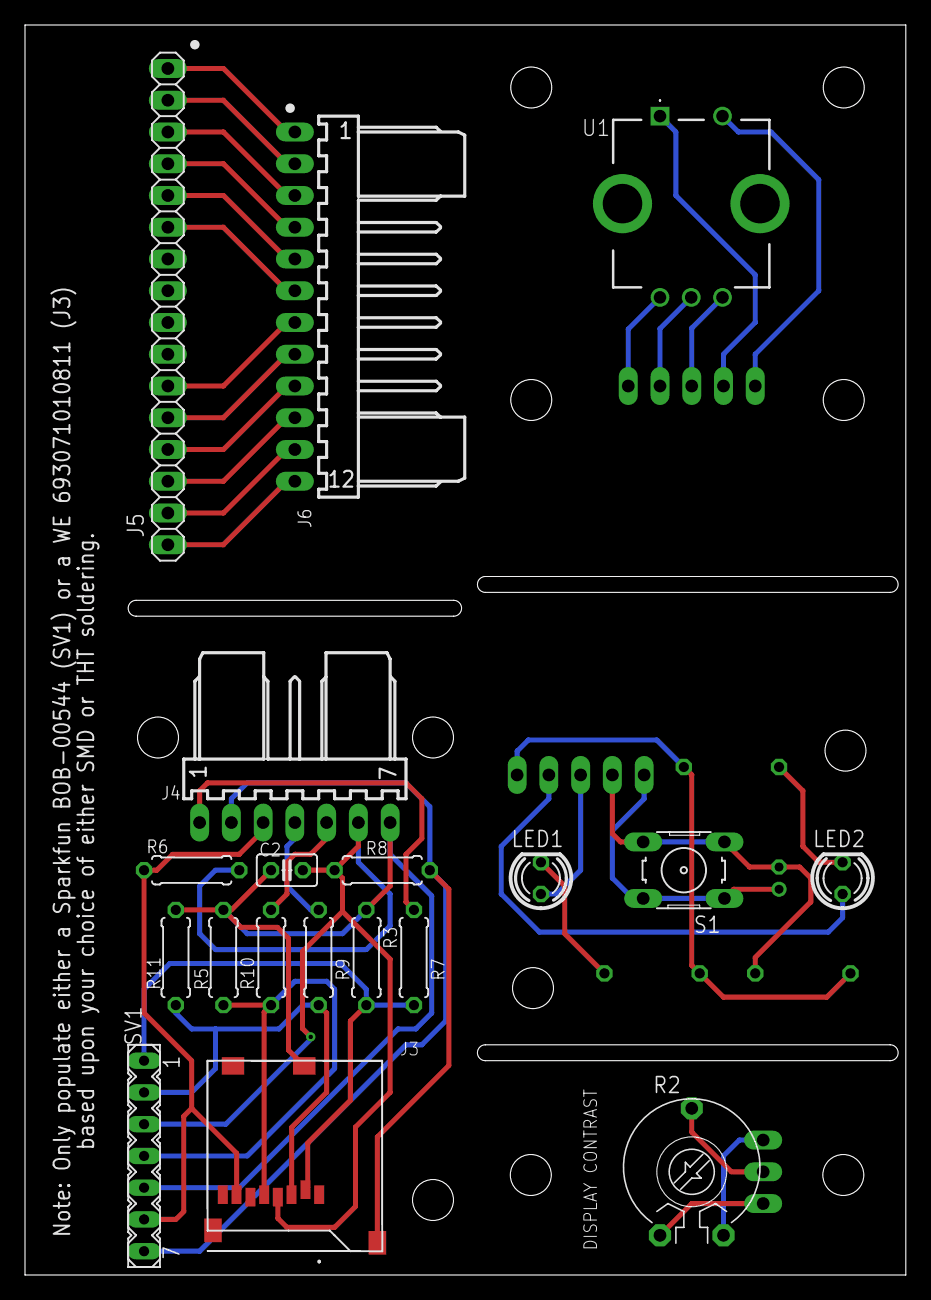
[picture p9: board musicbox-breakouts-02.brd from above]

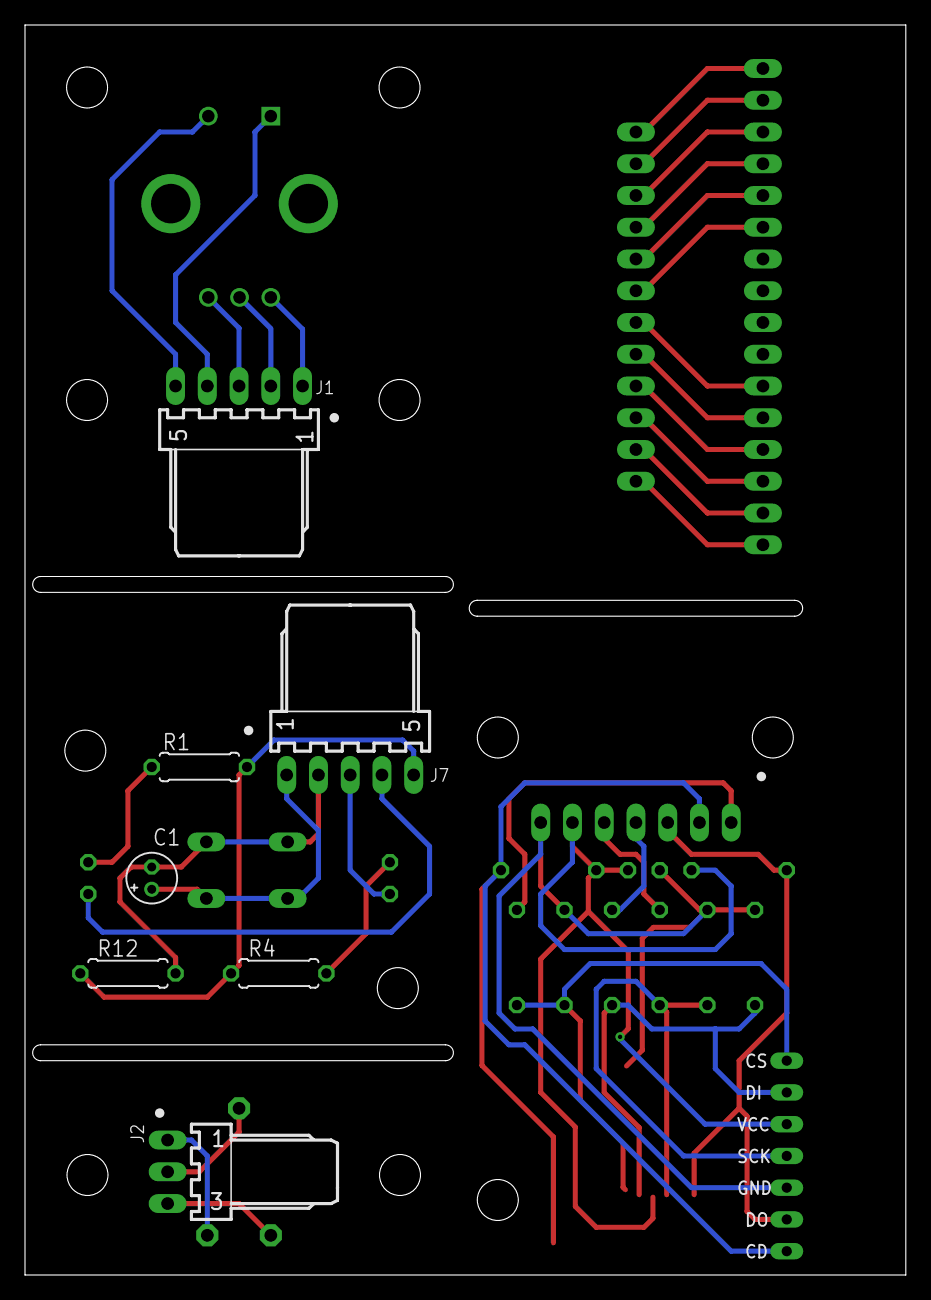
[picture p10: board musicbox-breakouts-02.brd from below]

Board: 2 copper layers, 70.5 x 100.0 mm, 26 parts (7 on the bottom side), 37 nets.

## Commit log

2022-07-05 added function to select servo order and used <fieldset>-tags for styling
2022-07-05 added eagle cad files
    [extra.csv, extra.xls, musicbox mechanical-02.brd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]
2022-07-07 added gerber files
    [musicbox.GBL, musicbox.GBO, musicbox.GBP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]
